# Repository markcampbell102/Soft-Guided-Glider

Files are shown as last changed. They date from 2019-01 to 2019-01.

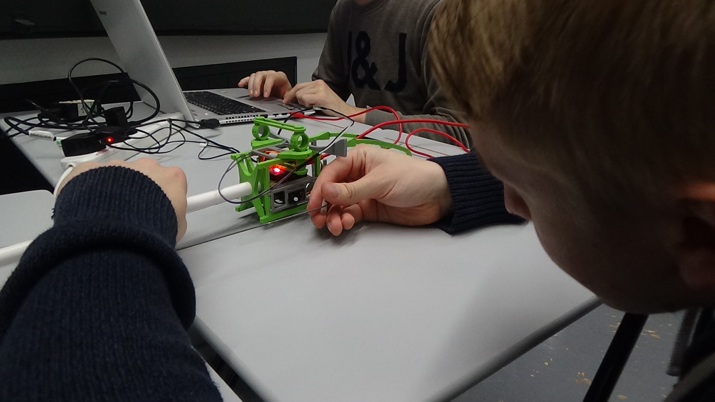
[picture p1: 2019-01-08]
Photos and Videos/Testing/DSC00016.JPG

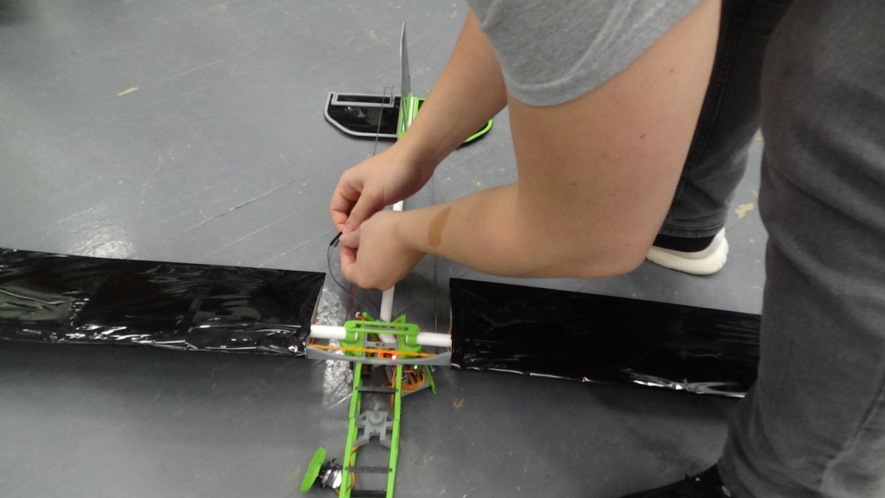
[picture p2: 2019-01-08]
Photos and Videos/Testing/DSC00044.JPG

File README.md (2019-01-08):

# The Soft Guided Glider

During disaster periods there are always areas which are more accessible from the air than from land due to damage to infrastructure after earthquakes or tsunamis. The purpose of this project was to build a low-cost glider that would be able to deliver vital supplies to people in need when they are in these difficult to reach locations. The Glider was designed to be compact, low cost, lightweight and soft. With these attributes it would be able to be thrown from a high altitude and land without damaging its intended cargo, the intended user or itself.

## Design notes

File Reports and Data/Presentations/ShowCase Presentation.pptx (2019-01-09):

## Soft Guided Glider

Andrew Brown, Connor Crabb-Thompson, Jeremy May, Mark Campbell

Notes: Jeremy

## Introduction

- Build a glider that can deliver vital supplies to people in need when they are in hard to reach locations

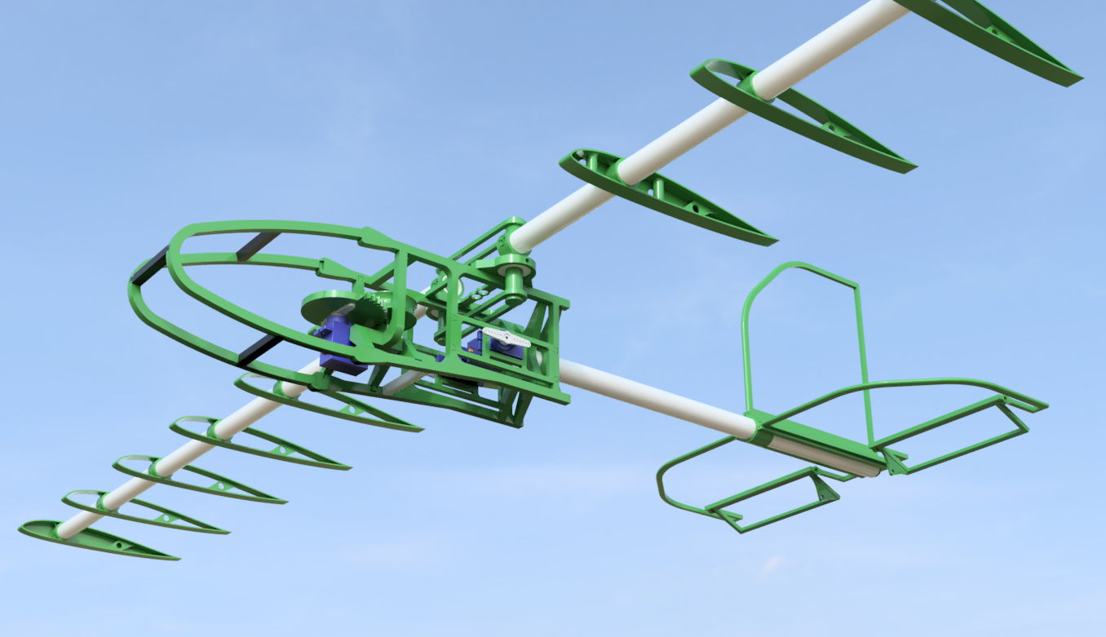
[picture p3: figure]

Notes: Jeremy

## Mechanical Design

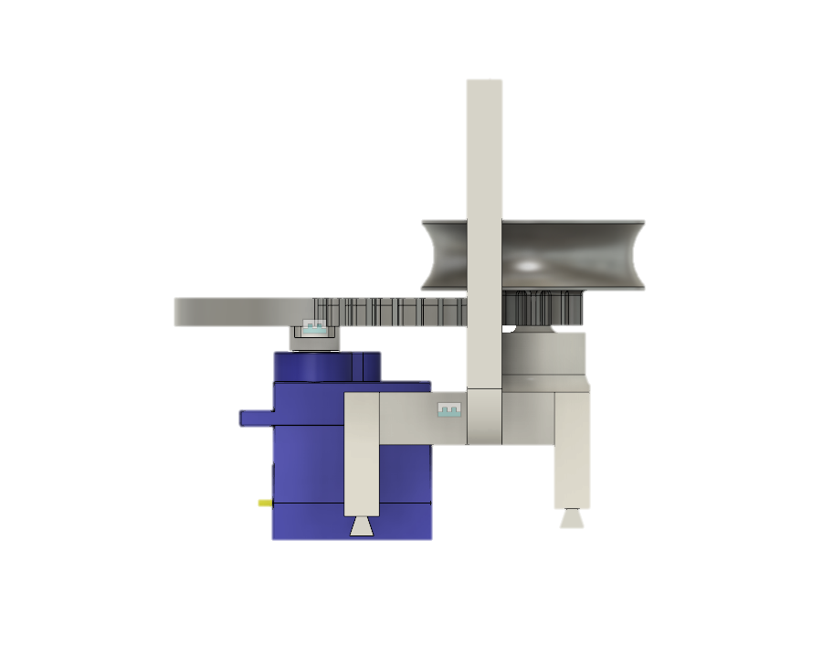
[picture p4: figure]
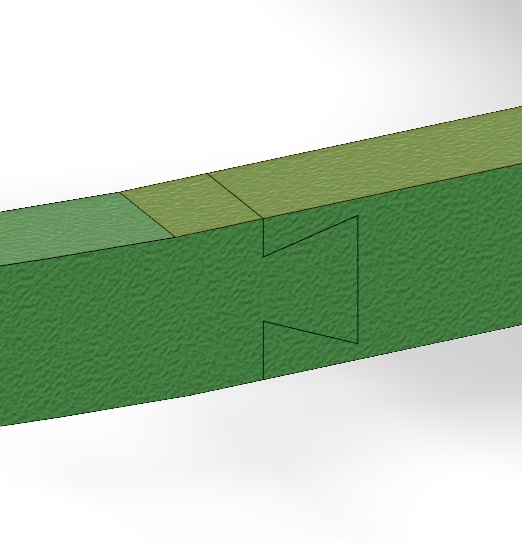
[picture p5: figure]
A picture containing stationary Description generated with very high confidence
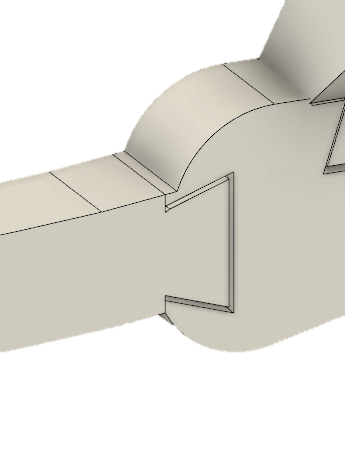
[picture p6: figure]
A picture containing object Description generated with high confidence
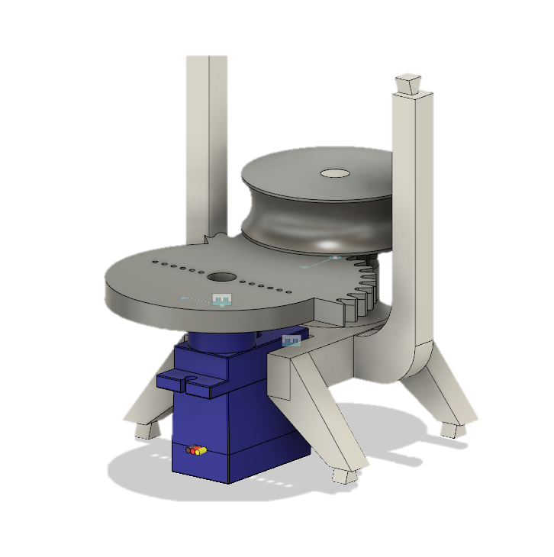
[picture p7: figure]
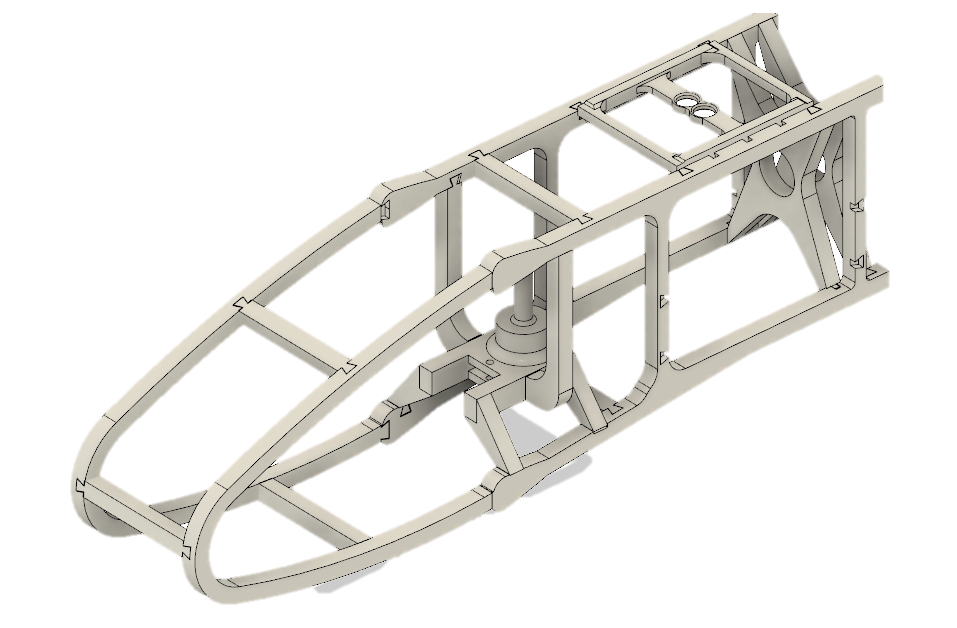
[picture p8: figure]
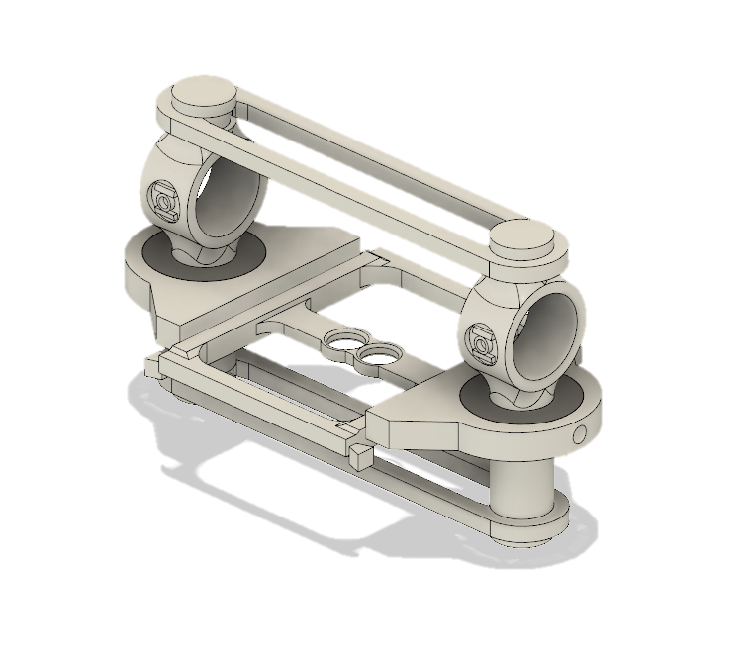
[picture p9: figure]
A picture containing LEGO, toy Description generated with very high confidence

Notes: Andrew

## Integrating Electronics

- Servo Housing has been built into system and connected to elevators
- Circuitry has been miniaturised onto Veroboard

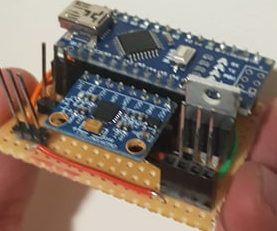
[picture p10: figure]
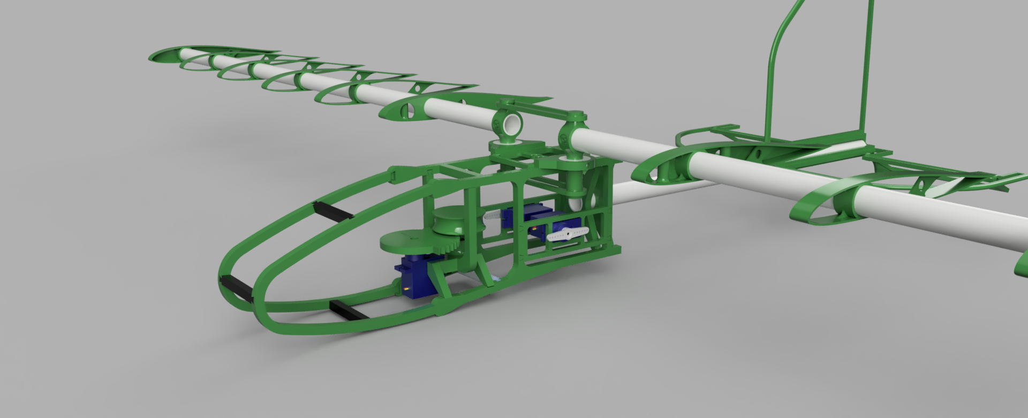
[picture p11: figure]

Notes: Connor

## Testing and Analysis

Analysis:
Finite element analysis

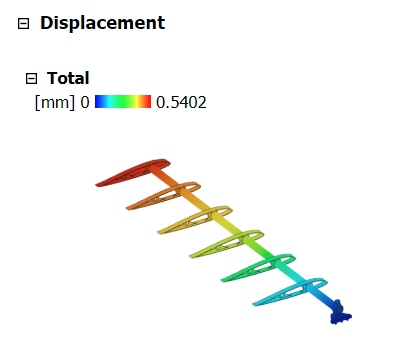
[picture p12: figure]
A close up of a logo Description generated with high confidence
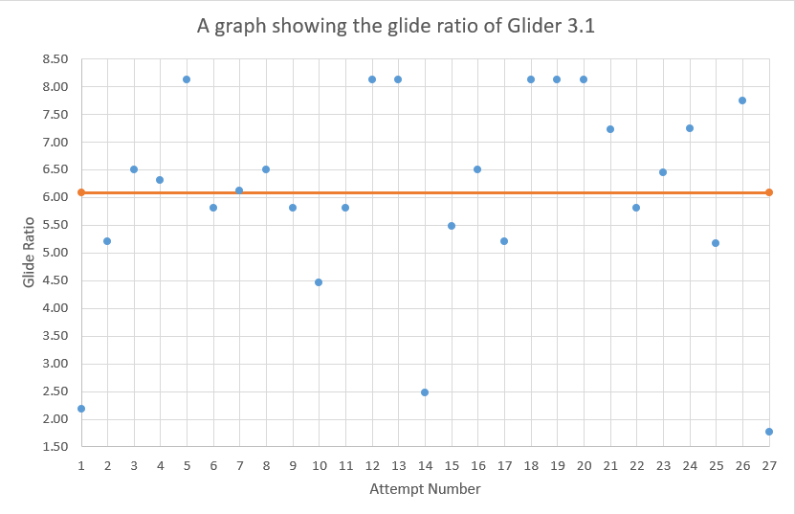
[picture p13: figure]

Testing:
Gliding testing
Compliancy testing
Steering testing

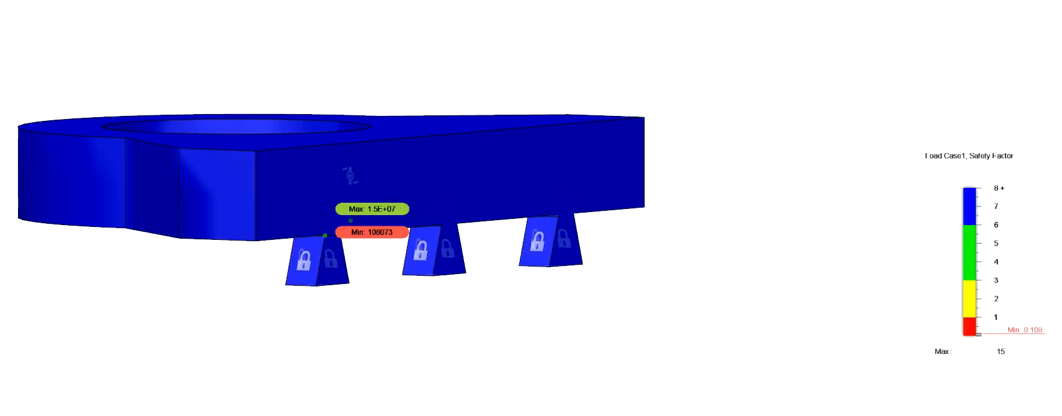
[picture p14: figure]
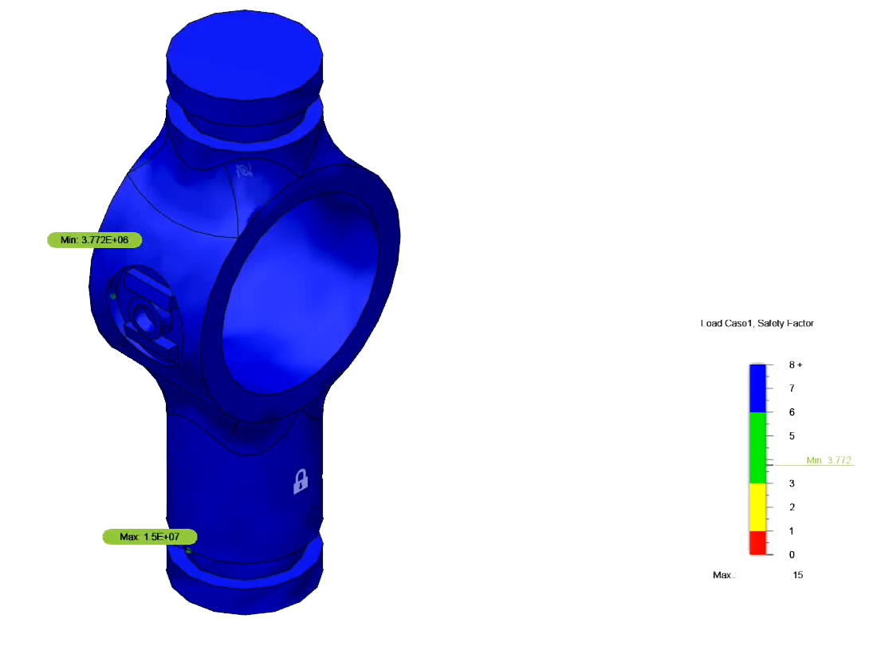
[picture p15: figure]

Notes: Mark

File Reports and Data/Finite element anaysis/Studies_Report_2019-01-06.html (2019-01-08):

Image Width (pixels):

# Wing FEA Report

Analyzed File | wing right v6
Version | Autodesk Fusion 360 (2.0.5119)
Creation Date | 2019-01-06, 12:41:29
Author | Andrew Brown, Mark Campbell

#### Project Properties

Title | Studies
Author | AndrewB

## Simulation Model 1:1

### Study 1 - Static Stress

##### Study Properties

Study Type | Static Stress
Last Modification Date | 2019-01-06, 12:38:17

#### Settings

##### General

Contact Tolerance | 0.1 mm
Remove Rigid Body Modes | No

##### Mesh

Average Element Size (% of model size)
Solids | 10
Scale Mesh Size Per Part | No
Average Element Size (absolute value) | -
Element Order | Parabolic
Create Curved Mesh Elements | Yes
Max. Turn Angle on Curves (Deg.) | 60
Max. Adjacent Mesh Size Ratio | 1.5
Max. Aspect Ratio | 10
Minimum Element Size (% of average size) | 20

##### Adaptive Mesh Refinement

Number of Refinement Steps | 0
Results Convergence Tolerance (%) | 20
Portion of Elements to Refine (%) | 10
Results for Baseline Accuracy | Von Mises Stress

#### Materials

Component | Material | Safety Factor
14mm x 600mm pvc pipe v1:1 | PVC-Piping | Yield Strength
wing 3 airfoil right end v1:1 | ABS Plastic | Yield Strength
wing 3 airfoil v1:1 | ABS Plastic | Yield Strength
wing 3 airfoil v1:2 | ABS Plastic | Yield Strength
wing 3 airfoil v1:3 | ABS Plastic | Yield Strength
wing 3 airfoil v1:4 | ABS Plastic | Yield Strength
wing 3 airfoil RIGHT START v3 v2:1 | ABS Plastic | Yield Strength

##### ABS Plastic

Density | 1.06E-06 kg / mm^3
Young's Modulus | 2240 MPa
Poisson's Ratio | 0.38
Yield Strength | 20 MPa
Ultimate Tensile Strength | 29.6 MPa
Thermal Conductivity | 1.6E-04 W / (mm C)
Thermal Expansion Coefficient | 8.57E-05 / C
Specific Heat | 1500 J / (kg C)

##### PVC-Piping

Density | 1.4E-06 kg / mm^3
Young's Modulus | 3400 MPa
Poisson's Ratio | 0.4
Yield Strength | 46.53 MPa
Ultimate Tensile Strength | 52.36 MPa
Thermal Conductivity | 0.001 W / (mm C)
Thermal Expansion Coefficient | 5E-07 / C
Specific Heat | 100 J / (kg C)

#### Contacts

##### Bonded

Name

[S] Bonded1 [14mm x 600mm pvc pipe v1:1||wing 3 airfoil right end v1:1]

[S] Bonded2 [14mm x 600mm pvc pipe v1:1||wing 3 airfoil RIGHT START v3 v2:1]

[S] Bonded3 [14mm x 600mm pvc pipe v1:1||wing 3 airfoil v1:4]

[S] Bonded4 [14mm x 600mm pvc pipe v1:1||wing 3 airfoil v1:3]

[S] Bonded5 [14mm x 600mm pvc pipe v1:1||wing 3 airfoil v1:2]

[S] Bonded6 [14mm x 600mm pvc pipe v1:1||wing 3 airfoil v1:1]

#### Mesh

Type | Nodes | Elements
Solids | 42074 | 19665

#### Load Case1

#### Constraints

##### Fixed1

Type | Fixed
Ux | Yes
Uy | Yes
Uz | Yes

###### Selected Entities

For correct interpretation of this image use e.g. IE9, Chrome, Safari, Firefox

#### Loads

##### Gravity

Type | Gravity
Magnitude | 9.807 m / s^2
X Value | 0 m / s^2
Y Value | -9.807 m / s^2
Z Value | 0 m / s^2

###### Selected Entities

For correct interpretation of this image use e.g. IE9, Chrome, Safari, Firefox

#### Results

##### Result Summary

Name | Minimum | Maximum
Safety Factor
Safety Factor (Per Body) | 15 | 15
Stress
Von Mises | 1.04E-06 MPa | 1.233 MPa
1st Principal | -0.4449 MPa | 1.876 MPa
3rd Principal | -1.423 MPa | 0.5272 MPa
Normal XX | -0.6099 MPa | 0.8494 MPa
Normal YY | -0.539 MPa | 0.6461 MPa
Normal ZZ | -1.383 MPa | 1.845 MPa
Shear XY | -0.1186 MPa | 0.09273 MPa
Shear YZ | -0.3367 MPa | 0.4469 MPa
Shear ZX | -0.3456 MPa | 0.3116 MPa
Displacement
Total | 0 mm | 1.149 mm
X | -2.596E-04 mm | 0.2115 mm
Y | -1.128 mm | 2.035E-05 mm
Z | -0.02293 mm | 0.06109 mm
Reaction Force
Total | 0 N | 1.872 N
X | -0.5288 N | 0.5612 N
Y | -0.9159 N | 1.152 N
Z | -1.37 N | 1.411 N
Strain
Equivalent | 7.027E-10 | 7.318E-04
1st Principal | 5.879E-10 | 8.061E-04
3rd Principal | -5.086E-04 | 4.124E-09
Normal XX | -8.495E-05 | 9.184E-05
Normal YY | -1.987E-04 | 1.058E-04
Normal ZZ | -4.224E-04 | 5.918E-04
Shear XY | -1.461E-04 | 1.143E-04
Shear YZ | -4.148E-04 | 4.401E-04
Shear ZX | -4.259E-04 | 3.839E-04
Contact Pressure
Total | 0 MPa | 0.5963 MPa
X | -0.07875 MPa | 0.08341 MPa
Y | -0.1702 MPa | 0.5621 MPa
Z | -0.1929 MPa | 0.1869 MPa

##### Safety Factor

###### Safety Factor (Per Body)

0 8

For correct interpretation of this image use e.g. IE9, Chrome, Safari, Firefox

##### Stress

###### Von Mises

[MPa] 0 1.233

For correct interpretation of this image use e.g. IE9, Chrome, Safari, Firefox

###### 1st Principal

[MPa] -0.445 1.876

For correct interpretation of this image use e.g. IE9, Chrome, Safari, Firefox

###### 3rd Principal

[MPa] -1.423 0.527

For correct interpretation of this image use e.g. IE9, Chrome, Safari, Firefox

##### Displacement

###### Total

[mm] 0 1.149

For correct interpretation of this image use e.g. IE9, Chrome, Safari, Firefox

Image Width (pixels):

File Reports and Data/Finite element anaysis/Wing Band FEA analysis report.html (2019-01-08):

Image Width (pixels):

# Wing Band FEA analysis report

Analyzed File | wing band v7
Version | Autodesk Fusion 360 (2.0.5119)
Creation Date | 2019-01-06, 11:46:38
Author | Andrew Brown, Mark Campbell

#### Project Properties

Title | Studies
Author | AndrewB

## Simulation Model 1:1

### Study 1 - Static Stress

##### Study Properties

Study Type | Static Stress
Last Modification Date | 2019-01-05, 18:14:45

#### Settings

##### General

Contact Tolerance | 0.1 mm
Remove Rigid Body Modes | No

##### Mesh

Average Element Size (% of model size)
Solids | 10
Scale Mesh Size Per Part | No
Average Element Size (absolute value) | -
Element Order | Parabolic
Create Curved Mesh Elements | Yes
Max. Turn Angle on Curves (Deg.) | 60
Max. Adjacent Mesh Size Ratio | 1.5
Max. Aspect Ratio | 10
Minimum Element Size (% of average size) | 20

##### Adaptive Mesh Refinement

Number of Refinement Steps | 0
Results Convergence Tolerance (%) | 20
Portion of Elements to Refine (%) | 10
Results for Baseline Accuracy | Von Mises Stress

#### Materials

Component | Material | Safety Factor
Body1 | ABS Plastic | Yield Strength

##### ABS Plastic

Density | 1.06E-06 kg / mm^3
Young's Modulus | 2240 MPa
Poisson's Ratio | 0.38
Yield Strength | 20 MPa
Ultimate Tensile Strength | 29.6 MPa
Thermal Conductivity | 1.6E-04 W / (mm C)
Thermal Expansion Coefficient | 8.57E-05 / C
Specific Heat | 1500 J / (kg C)

#### Contacts

#### Mesh

Type | Nodes | Elements
Solids | 2045 | 1021

#### Load Case1

#### Constraints

##### Fixed1

Type | Fixed
Ux | Yes
Uy | Yes
Uz | Yes

###### Selected Entities

For correct interpretation of this image use e.g. IE9, Chrome, Safari, Firefox

#### Loads

##### Force1

Type | Force
Magnitude | 12 N
X Value | -12 N
Y Value | 0 N
Z Value | 0 N
X Angle | 0 deg
Y Angle | 0 deg
Z Angle | 0 deg
Force Per Entity | No

###### Selected Entities

For correct interpretation of this image use e.g. IE9, Chrome, Safari, Firefox

##### Force2

Type | Force
Magnitude | 12 N
X Value | 12 N
Y Value | 0 N
Z Value | 0 N
X Angle | 0 deg
Y Angle | 0 deg
Z Angle | 0 deg
Force Per Entity | No

###### Selected Entities

For correct interpretation of this image use e.g. IE9, Chrome, Safari, Firefox

#### Results

##### Result Summary

Name | Minimum | Maximum
Safety Factor
Safety Factor (Per Body) | 15 | 15
Stress
Von Mises | 2.283E-06 MPa | 0.6002 MPa
1st Principal | -0.1353 MPa | 0.6666 MPa
3rd Principal | -0.5343 MPa | 0.1268 MPa
Normal XX | -0.3974 MPa | 0.6541 MPa
Normal YY | -0.4178 MPa | 0.4562 MPa
Normal ZZ | -0.2417 MPa | 0.2879 MPa
Shear XY | -0.3285 MPa | 0.3107 MPa
Shear YZ | -0.05948 MPa | 0.06786 MPa
Shear ZX | -0.2087 MPa | 0.2208 MPa
Displacement
Total | 0 mm | 9.274E-04 mm
X | -8.42E-04 mm | 8.679E-04 mm
Y | -2.073E-04 mm | 3.267E-04 mm
Z | -2.113E-04 mm | 1.965E-04 mm
Reaction Force
Total | 0 N | 1.06 N
X | -0.9213 N | 0.8655 N
Y | -0.6553 N | 0.6005 N
Z | -0.1777 N | 0.1644 N
Strain
Equivalent | 1.816E-09 | 4.677E-04
1st Principal | 1.214E-09 | 4.145E-04
3rd Principal | -3.953E-04 | -1.838E-09
Normal XX | -1.701E-04 | 2.668E-04
Normal YY | -1.081E-04 | 1.167E-04
Normal ZZ | -1.094E-04 | 6.626E-05
Shear XY | -4.048E-04 | 3.828E-04
Shear YZ | -7.329E-05 | 8.361E-05
Shear ZX | -2.572E-04 | 2.72E-04

##### Safety Factor

###### Safety Factor (Per Body)

0 8

For correct interpretation of this image use e.g. IE9, Chrome, Safari, Firefox

##### Stress

###### Von Mises

[MPa] 0 0.6002

For correct interpretation of this image use e.g. IE9, Chrome, Safari, Firefox

###### 1st Principal

[MPa] -0.1353 0.6666

For correct interpretation of this image use e.g. IE9, Chrome, Safari, Firefox

###### 3rd Principal

[MPa] -0.5343 0.1268

For correct interpretation of this image use e.g. IE9, Chrome, Safari, Firefox

##### Displacement

###### Total

[mm] 0 9.274E-04

For correct interpretation of this image use e.g. IE9, Chrome, Safari, Firefox

Image Width (pixels):

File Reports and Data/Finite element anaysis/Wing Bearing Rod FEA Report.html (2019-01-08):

Image Width (pixels):

# Wing Bearing Rod FEA Report

Analyzed File | green lantern v11
Version | Autodesk Fusion 360 (2.0.5119)
Creation Date | 2019-01-06, 11:47:30
Author | Andrew Brown, Mark Campbell

#### Project Properties

Title | Studies
Author | mqcampbell

## Simulation Model 1:1

### Study 2 - Static Stress

##### Study Properties

Study Type | Static Stress
Last Modification Date | 2019-01-05, 18:17:33

#### Settings

##### General

Contact Tolerance | 0.1 mm
Remove Rigid Body Modes | No

##### Mesh

Average Element Size (% of model size)
Solids | 10
Scale Mesh Size Per Part | No
Average Element Size (absolute value) | -
Element Order | Parabolic
Create Curved Mesh Elements | Yes
Max. Turn Angle on Curves (Deg.) | 60
Max. Adjacent Mesh Size Ratio | 1.5
Max. Aspect Ratio | 10
Minimum Element Size (% of average size) | 20

##### Adaptive Mesh Refinement

Number of Refinement Steps | 0
Results Convergence Tolerance (%) | 20
Portion of Elements to Refine (%) | 10
Results for Baseline Accuracy | Von Mises Stress

#### Materials

Component | Material | Safety Factor
Body1 | ABS Plastic | Yield Strength

##### ABS Plastic

Density | 1.06E-06 kg / mm^3
Young's Modulus | 2240 MPa
Poisson's Ratio | 0.38
Yield Strength | 20 MPa
Ultimate Tensile Strength | 29.6 MPa
Thermal Conductivity | 1.6E-04 W / (mm C)
Thermal Expansion Coefficient | 8.57E-05 / C
Specific Heat | 1500 J / (kg C)

#### Contacts

#### Mesh

Type | Nodes | Elements
Solids | 2573 | 1341

#### Load Case1

#### Constraints

##### Fixed1

Type | Fixed
Ux | Yes
Uy | Yes
Uz | Yes

###### Selected Entities

For correct interpretation of this image use e.g. IE9, Chrome, Safari, Firefox

#### Loads

##### Moment1

Type | Moment
Magnitude | 192 N mm
X Value | -192 N mm
Y Value | 0 N mm
Z Value | 4.263E-14 N mm
X Angle | 0 deg
Y Angle | 0 deg
Z Angle | 0 deg

###### Selected Entities

For correct interpretation of this image use e.g. IE9, Chrome, Safari, Firefox

#### Results

##### Result Summary

Name | Minimum | Maximum
Safety Factor
Safety Factor (Per Body) | 4.491 | 15
Stress
Von Mises | 3.796E-08 MPa | 4.453 MPa
1st Principal | -0.7836 MPa | 4.472 MPa
3rd Principal | -4.612 MPa | 0.7673 MPa
Normal XX | -1.626 MPa | 1.665 MPa
Normal YY | -4.027 MPa | 4.138 MPa
Normal ZZ | -2.213 MPa | 2.249 MPa
Shear XY | -1.634 MPa | 1.558 MPa
Shear YZ | -1.694 MPa | 1.106 MPa
Shear ZX | -1.276 MPa | 1.217 MPa
Displacement
Total | 0 mm | 0.1566 mm
X | -0.01783 mm | 0.01843 mm
Y | -0.0398 mm | 0.03999 mm
Z | -0.1523 mm | 3.496E-04 mm
Reaction Force
Total | 0 N | 4.381 N
X | -2.166 N | 2.091 N
Y | -3.311 N | 3.846 N
Z | -1.247 N | 1.963 N
Strain
Equivalent | 2.663E-11 | 0.003043
1st Principal | 2.219E-11 | 0.002726
3rd Principal | -0.003147 | -2.207E-11
Normal XX | -7.456E-04 | 7.316E-04
Normal YY | -0.001668 | 0.00174
Normal ZZ | -6.567E-04 | 7.107E-04
Shear XY | -0.002013 | 0.00192
Shear YZ | -0.002088 | 0.001363
Shear ZX | -0.001572 | 0.001499

##### Safety Factor

###### Safety Factor (Per Body)

0 8

For correct interpretation of this image use e.g. IE9, Chrome, Safari, Firefox

##### Stress

###### Von Mises

[MPa] 0 4.453

For correct interpretation of this image use e.g. IE9, Chrome, Safari, Firefox

###### 1st Principal

[MPa] -0.784 4.472

For correct interpretation of this image use e.g. IE9, Chrome, Safari, Firefox

###### 3rd Principal

[MPa] -4.612 0.767

For correct interpretation of this image use e.g. IE9, Chrome, Safari, Firefox

##### Displacement

###### Total

[mm] 0 0.1566

For correct interpretation of this image use e.g. IE9, Chrome, Safari, Firefox

Image Width (pixels):

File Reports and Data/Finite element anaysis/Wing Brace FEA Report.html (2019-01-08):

Image Width (pixels):

# wing brace FEA report

Analyzed File | wing brace v10
Version | Autodesk Fusion 360 (2.0.5119)
Creation Date | 2019-01-06, 13:33:17
Author | Andrew Brown, Mark Campbell

#### Project Properties

Title | Studies
Author | AndrewB

## Simulation Model 1:1

### Study 2 - Static Stress

##### Study Properties

Study Type | Static Stress
Last Modification Date | 2019-01-06, 13:30:13

#### Settings

##### General

Contact Tolerance | 0.1 mm
Remove Rigid Body Modes | No

##### Mesh

Average Element Size (% of model size)
Solids | 10
Scale Mesh Size Per Part | No
Average Element Size (absolute value) | -
Element Order | Parabolic
Create Curved Mesh Elements | Yes
Max. Turn Angle on Curves (Deg.) | 60
Max. Adjacent Mesh Size Ratio | 1.5
Max. Aspect Ratio | 10
Minimum Element Size (% of average size) | 20

##### Adaptive Mesh Refinement

Number of Refinement Steps | 0
Results Convergence Tolerance (%) | 20
Portion of Elements to Refine (%) | 10
Results for Baseline Accuracy | Von Mises Stress

#### Materials

Component | Material | Safety Factor
Body5 | ABS Plastic | Yield Strength

##### ABS Plastic

Density | 1.06E-06 kg / mm^3
Young's Modulus | 2240 MPa
Poisson's Ratio | 0.38
Yield Strength | 20 MPa
Ultimate Tensile Strength | 29.6 MPa
Thermal Conductivity | 1.6E-04 W / (mm C)
Thermal Expansion Coefficient | 8.57E-05 / C
Specific Heat | 1500 J / (kg C)

#### Contacts

#### Mesh

Type | Nodes | Elements
Solids | 12501 | 7020

#### Load Case1

#### Constraints

##### Fixed2

Type | Fixed
Ux | Yes
Uy | Yes
Uz | Yes

###### Selected Entities

For correct interpretation of this image use e.g. IE9, Chrome, Safari, Firefox

#### Loads

##### Gravity

Type | Gravity
Magnitude | 9.807 m / s^2
X Value | 0 m / s^2
Y Value | -9.807 m / s^2
Z Value | 0 m / s^2

###### Selected Entities

For correct interpretation of this image use e.g. IE9, Chrome, Safari, Firefox

##### Force1

Type | Force
Magnitude | 1 N
X Value | 0 N
Y Value | 0 N
Z Value | 1 N
Force Per Entity | No

###### Selected Entities

For correct interpretation of this image use e.g. IE9, Chrome, Safari, Firefox

#### Results

##### Result Summary

Name | Minimum | Maximum
Safety Factor
Safety Factor (Per Body) | 15 | 15
Stress
Von Mises | 1.461E-18 MPa | 0.7413 MPa
1st Principal | -0.0411 MPa | 0.9361 MPa
3rd Principal | -0.4175 MPa | 0.3906 MPa
Normal XX | -0.2087 MPa | 0.5432 MPa
Normal YY | -0.2808 MPa | 0.5742 MPa
Normal ZZ | -0.4055 MPa | 0.6938 MPa
Shear XY | -0.1047 MPa | 0.07226 MPa
Shear YZ | -0.2261 MPa | 0.1931 MPa
Shear ZX | -0.1428 MPa | 0.1479 MPa
Displacement
Total | 0 mm | 0.06755 mm
X | -0.001484 mm | 1.382E-04 mm
Y | -3.579E-04 mm | 0.06277 mm
Z | -0.0246 mm | 0.02499 mm
Reaction Force
Total | 0 N | 0.2882 N
X | -0.03586 N | 0.04169 N
Y | -0.04169 N | 0.08177 N
Z | -0.2768 N | 0.282 N
Strain
Equivalent | 0 | 4.135E-04
1st Principal | 0 | 4.571E-04
3rd Principal | -2.445E-04 | 0
Normal XX | -9.423E-05 | 6.521E-05
Normal YY | -1.871E-04 | 6.47E-05
Normal ZZ | -1.702E-04 | 2.8E-04
Shear XY | -1.29E-04 | 8.904E-05
Shear YZ | -2.786E-04 | 2.38E-04
Shear ZX | -1.76E-04 | 1.823E-04

##### Safety Factor

###### Safety Factor (Per Body)

0 8

For correct interpretation of this image use e.g. IE9, Chrome, Safari, Firefox

##### Stress

###### Von Mises

[MPa] 0 0.7413

For correct interpretation of this image use e.g. IE9, Chrome, Safari, Firefox

###### 1st Principal

[MPa] -0.0411 0.9361

For correct interpretation of this image use e.g. IE9, Chrome, Safari, Firefox

###### 3rd Principal

[MPa] -0.4175 0.3906

For correct interpretation of this image use e.g. IE9, Chrome, Safari, Firefox

##### Displacement

###### Total

[mm] 0 0.06755

For correct interpretation of this image use e.g. IE9, Chrome, Safari, Firefox

Image Width (pixels):

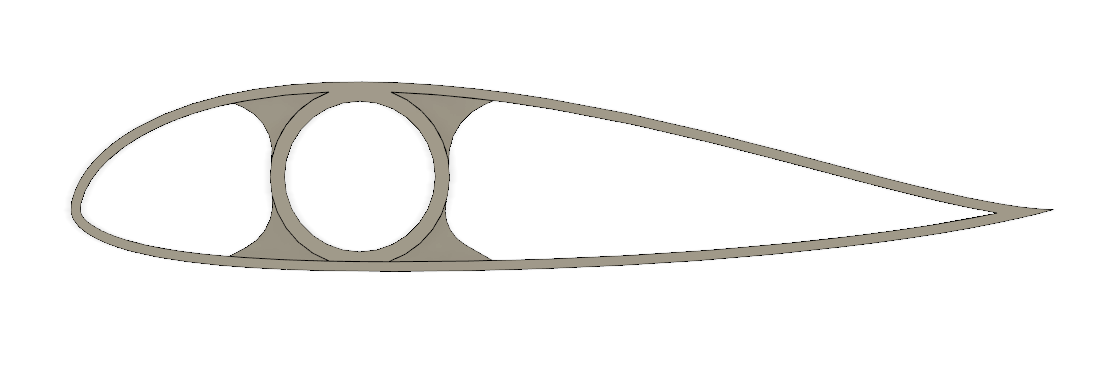
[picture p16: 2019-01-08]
Photos and Videos/Mechanical Models/Aerofoil/prototype/Aerofoil 1 side.PNG

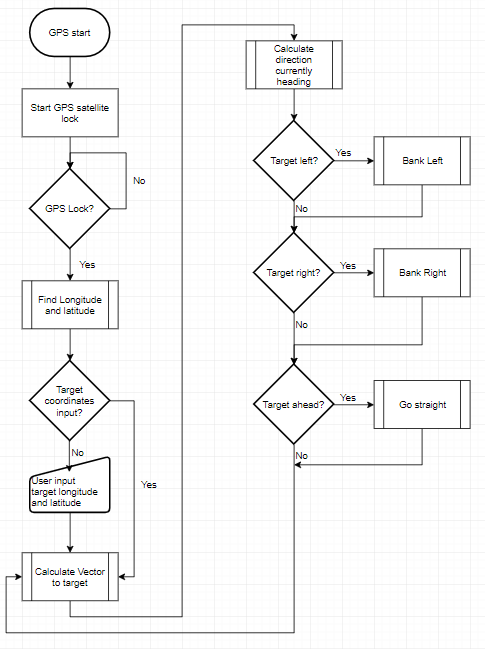
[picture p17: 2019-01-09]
Electronics/Localisation/GPS Flowchart.PNG

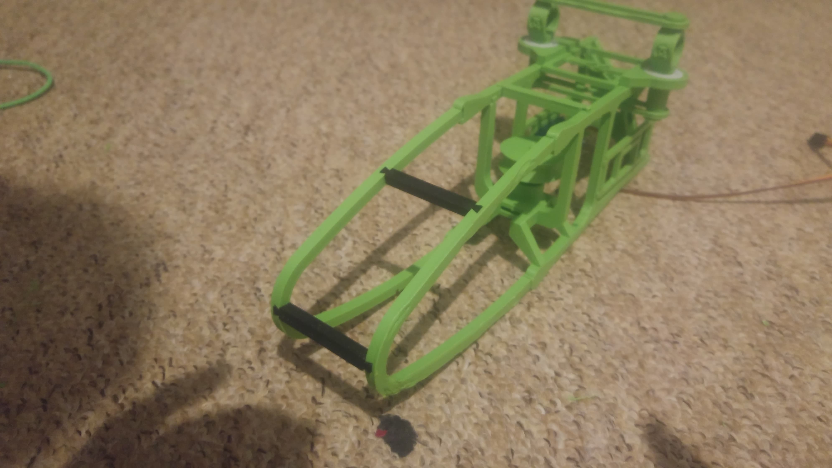
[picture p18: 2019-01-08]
Photos and Videos/Mechanical Models/Body/body v3/49678581_937155589824171_4841866462714920960_n.jpg

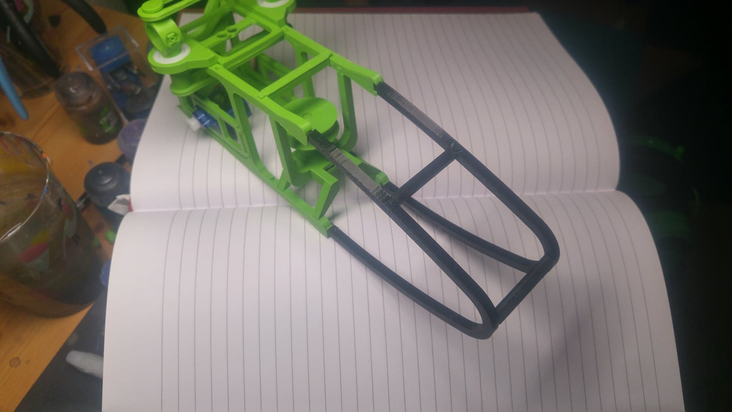
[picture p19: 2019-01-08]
Photos and Videos/Mechanical Models/Body/body v3/49845082_1233951370087210_7048269515758501888_n.jpg

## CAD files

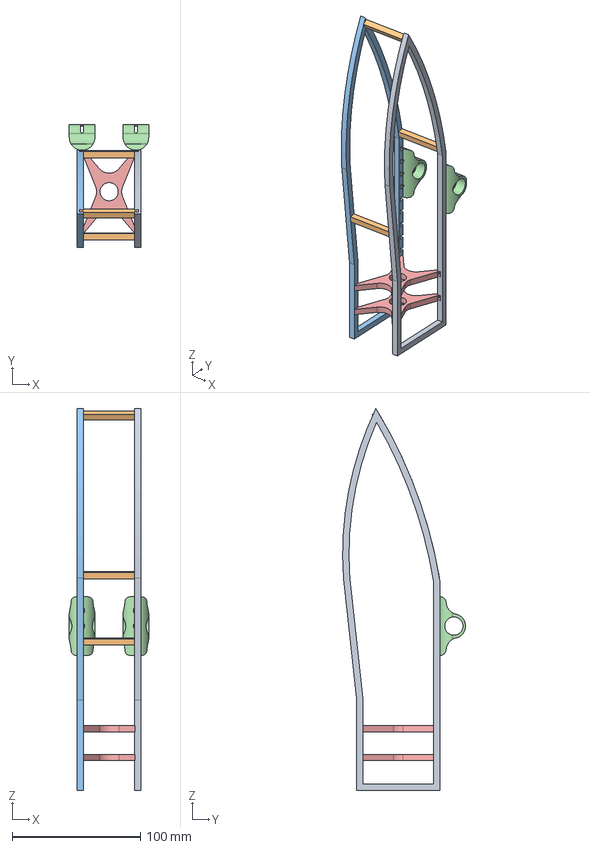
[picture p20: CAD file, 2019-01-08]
Mechanicals/assembalies/body 2/body assembly 2.stp
62.0 x 95.8 x 297.9 mm
body side mirrored v3 x 2
standard strut x 3
body side
wing attachment x 2
x beam x 2

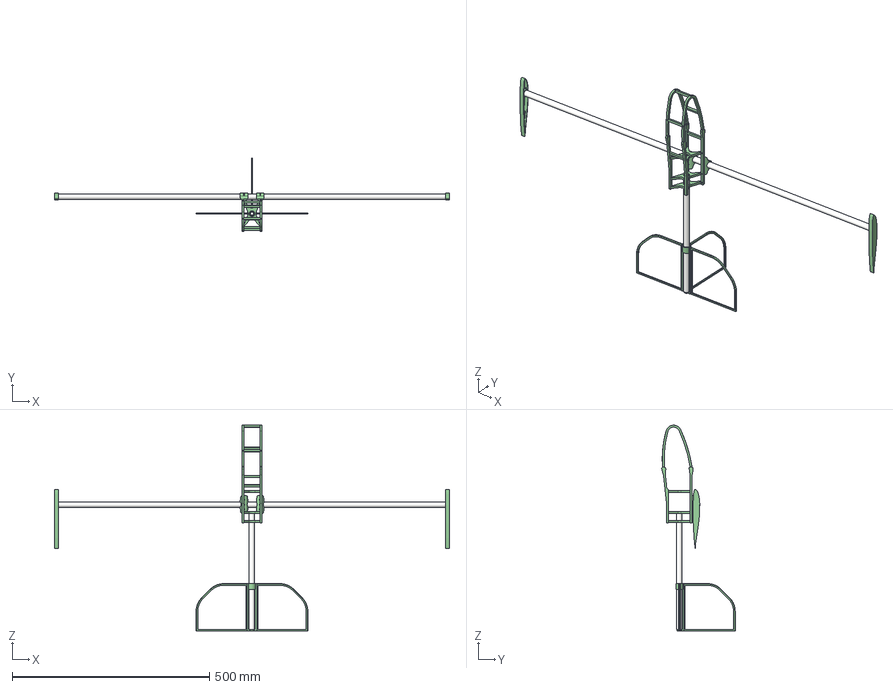
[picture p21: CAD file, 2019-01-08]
Mechanicals/assembalies/body 3.1/Test assembly.stp
1002.0 x 186.6 x 522.0 mm
body right side back
body side right front
x beam x 3
body left side back
body side left front
standard strut x 5
wing attachment x 2
14mm x 1000mm rod
wing 3 airfoil left end
wing 3 airfoil right end
14mmx 300mm
rod attachment 2
horzontal fin x 3

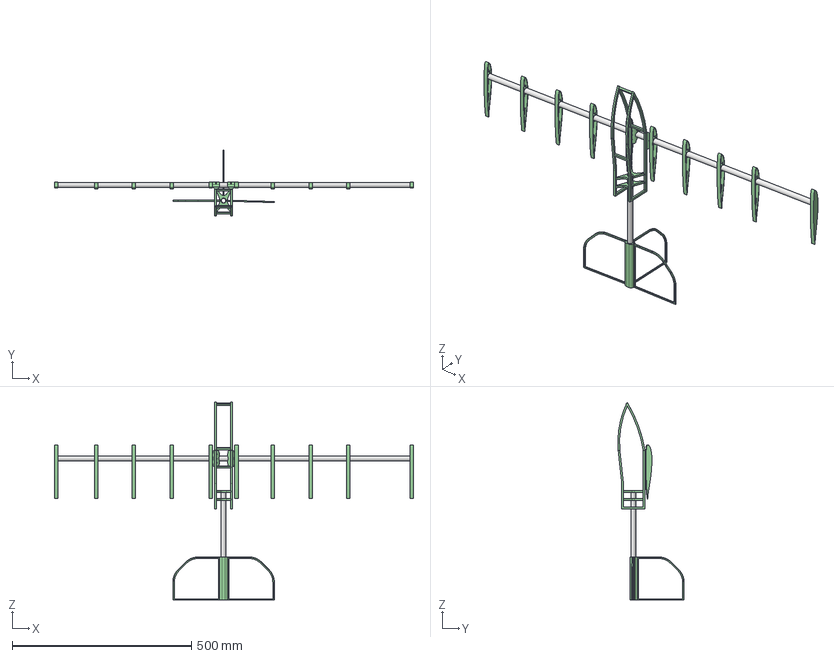
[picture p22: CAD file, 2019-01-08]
Mechanicals/assembalies/body 3/assembly 3.stp
1002.0 x 185.1 x 552.1 mm
body left side back
body side left front
standard strut x 3
x beam x 2
body right side back
body side right front
wing attachment x 2
14mm x 1000mm rod
wing 3 airfoil x 8
wing 3 airfoil right end
wing 3 airfoil left end
14mmx 300mm
rod attachment
horzontal fin x 3

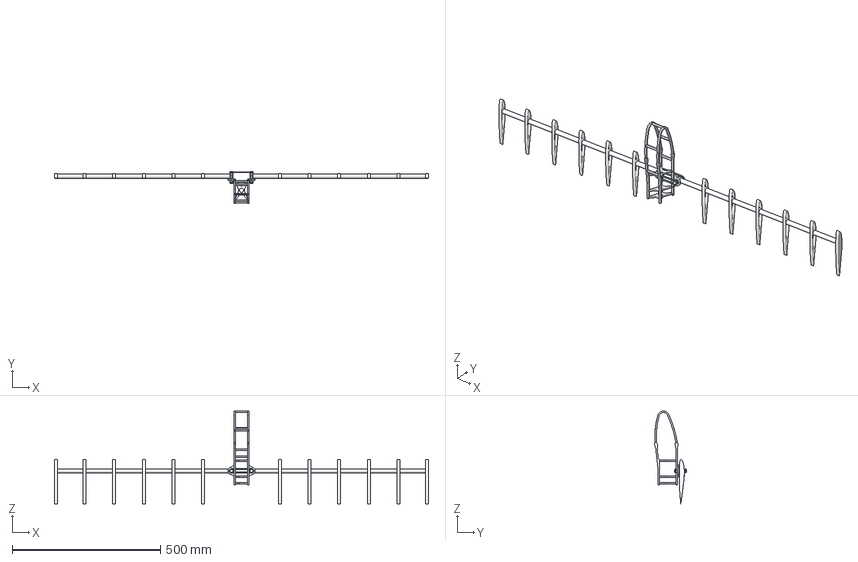
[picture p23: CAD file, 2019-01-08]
Mechanicals/assembalies/body 4/Assembly 5.stp
1259.9 x 108.2 x 313.0 mm
body left side back v2
body side left front v2
standard strut v2 x 5
x beam v3 x 3
body side right front v2
body right side back v2
wing bearing mount right v7 x 2
10mm x 15mm x 4mm bearing v1 x 2
green lantern v4 x 2
wing band v2 x 2
14mm x 600mm pvc pipe v1 x 2
wing 3 airfoil right end v1
wing 3 airfoil v1 x 10
wing 3 airfoil left end v3

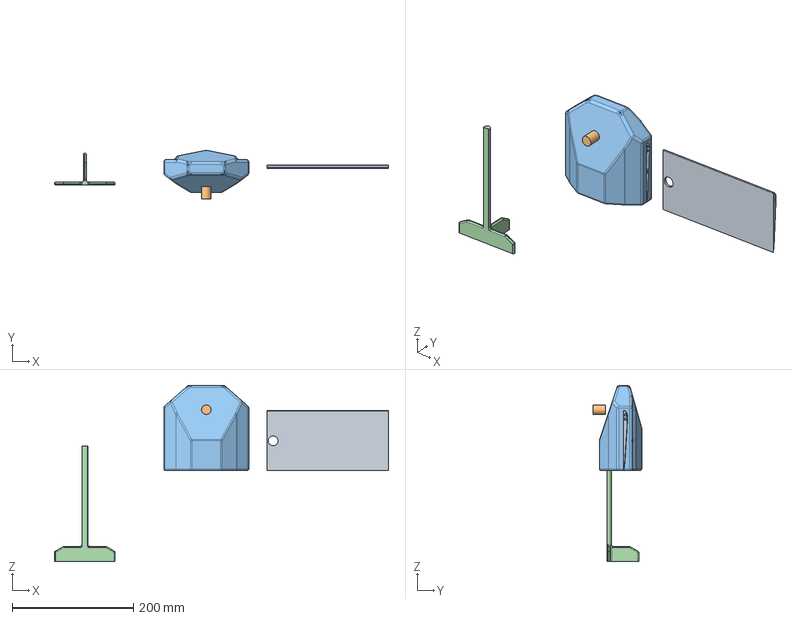
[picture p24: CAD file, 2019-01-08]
Mechanicals/Body/body 1/Body Main.stp
550.0 x 79.9 x 290.0 mm
wing mount point mirror
Pin

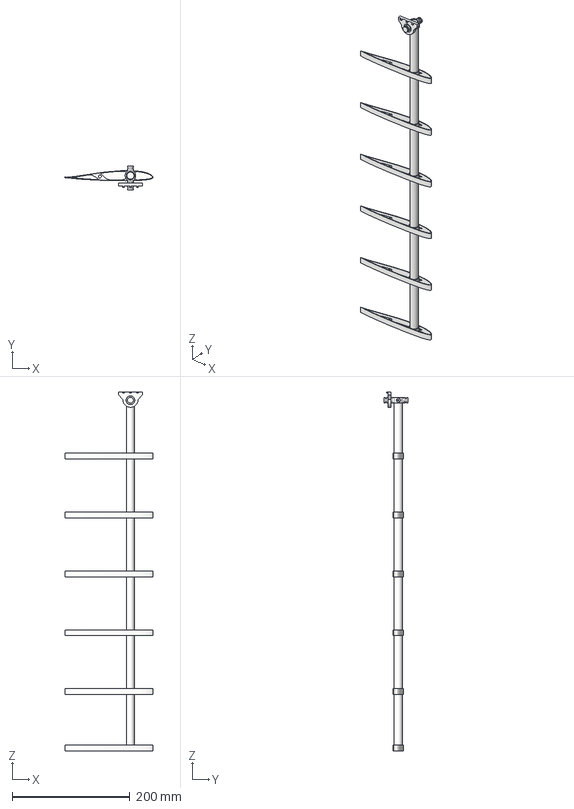
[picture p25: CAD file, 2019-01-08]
Mechanicals/Simulation/Wing Hing assembly.stp
150.0 x 40.0 x 610.0 mm
green lantern v7
14mm x 600mm pvc pipe v1
wing 3 airfoil left end v3
wing 3 airfoil v1 x 5
wing bearing mount right v11
10mm x 15mm x 4mm bearing v1

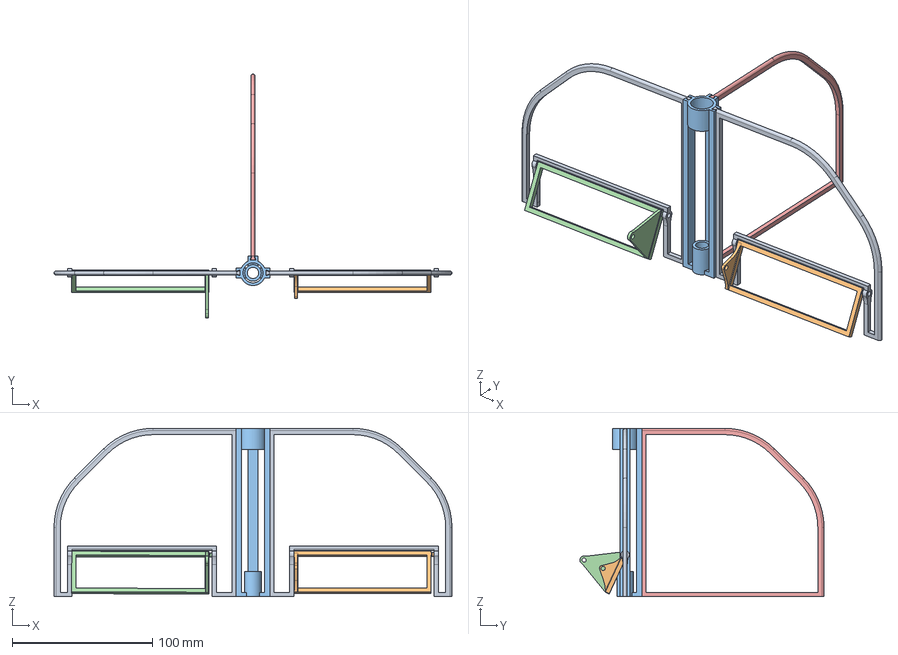
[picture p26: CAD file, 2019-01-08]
Mechanicals/Tails/tail 2/assembly.stp
283.8 x 174.1 x 120.0 mm
vertical fin x 2
horizontal move fin right
rod attachment 2
horizontal move fin left
horzontal fin

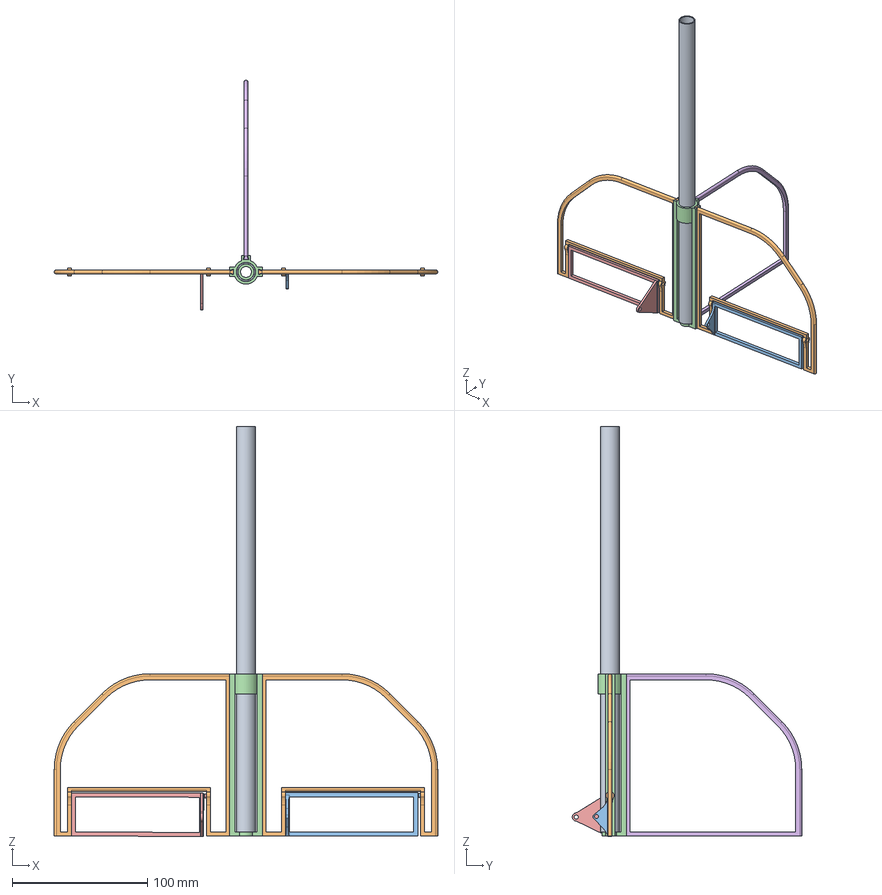
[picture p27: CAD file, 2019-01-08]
Mechanicals/Tails/tail 2/tail assembly full.stp
283.8 x 169.9 x 303.4 mm
14mmx 300mm
vertical fin x 2
horizontal move fin right
rod attachment 2
horizontal move fin left
horzontal fin

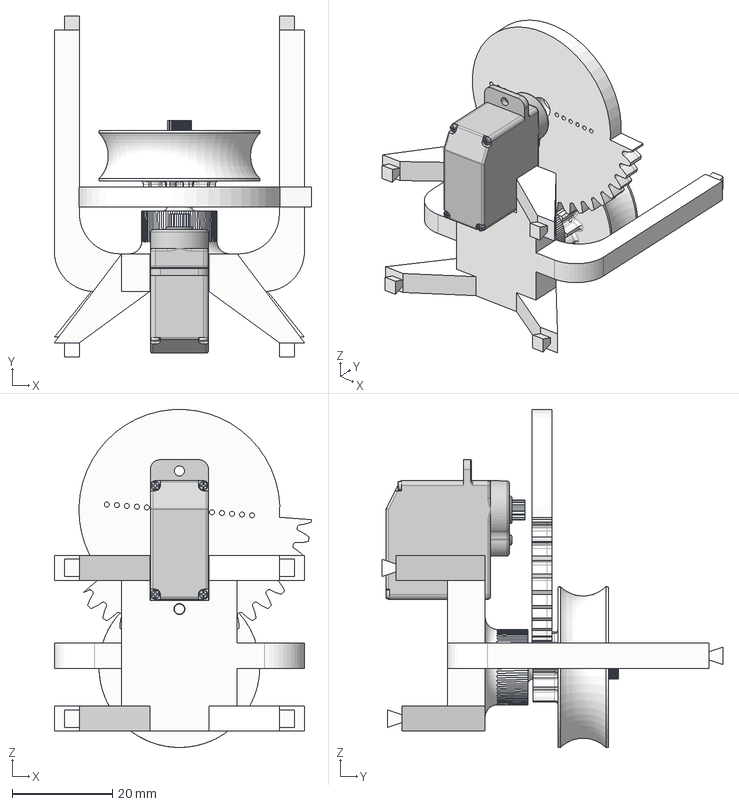
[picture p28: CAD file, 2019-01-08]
Mechanicals/assembalies/folder servo mount.stp
51.2 x 67.8 x 67.3 mm
folding gear mount
Spur Gear (42 teeth)
Emax ES08A

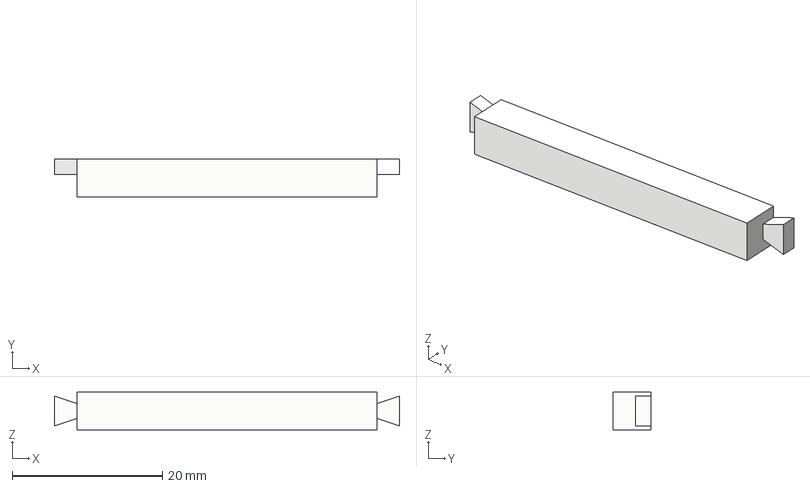
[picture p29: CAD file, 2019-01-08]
Mechanicals/Body/Body 2/standard strut.stp
46.0 x 5.00 x 5.00 mm

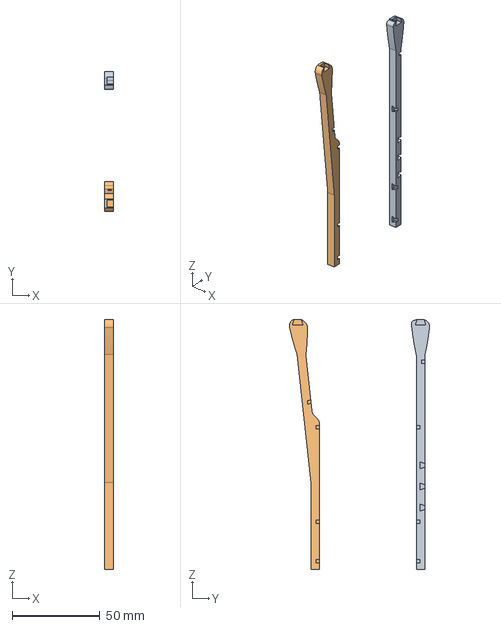
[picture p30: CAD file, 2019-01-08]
Mechanicals/Body/Body 3.1/body right side back.stp
5.00 x 79.8 x 142.2 mm

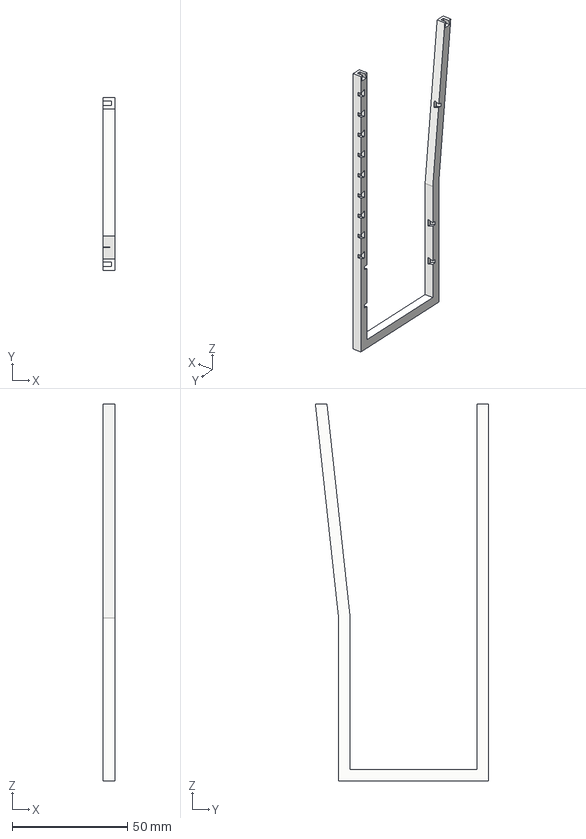
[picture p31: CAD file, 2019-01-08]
Mechanicals/Body/Body 3/body left side back.stp
5.00 x 75.0 x 163.2 mm

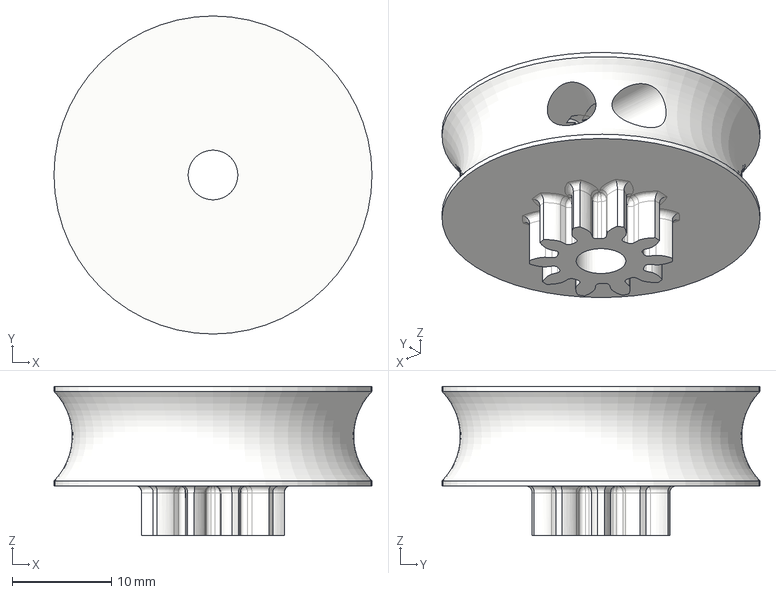
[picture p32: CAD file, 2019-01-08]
Mechanicals/Body/body 4/driven gear.stp
32.0 x 32.0 x 15.0 mm

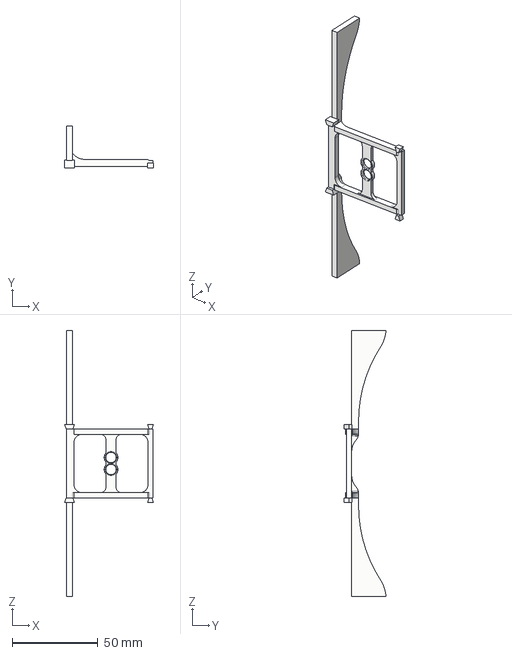
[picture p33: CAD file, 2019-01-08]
Mechanicals/Body/body 5/wing brace.stp
51.8 x 24.5 x 154.9 mm

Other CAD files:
Mechanicals/downloads/9g servo.stp
Mechanicals/Final 3D Model/Parts/servos/9g servo.stp
Mechanicals/Final 3D Model/Parts/wings/wing 3 airfoil RIGHT START v3.stp
Mechanicals/Body/Body 2/body right side front.obj
Mechanicals/Body/Body 2/body right side front.stp
Mechanicals/Body/Body 2/body side (1).obj
Mechanicals/Body/Body 2/body side (1).stp
Mechanicals/Body/Body 2/body side mirrored v3.obj
Mechanicals/Body/Body 2/body side mirrored v3.stp
Mechanicals/Body/Body 2/body side.obj
Mechanicals/Body/Body 2/body side.stp
Mechanicals/Body/Body 2/standard strut.obj
Mechanicals/Body/Body 2/wing attachment.obj
Mechanicals/Body/Body 2/wing attachment.stp
Mechanicals/Body/Body 2/x beam.obj
Mechanicals/Body/Body 2/x beam.stp
Mechanicals/Body/Body 3.1/body left side back.obj
Mechanicals/Body/Body 3.1/body left side back.stp
Mechanicals/Body/Body 3.1/body right side back.obj
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

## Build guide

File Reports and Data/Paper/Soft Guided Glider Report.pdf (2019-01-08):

# The Soft Guided Glider

Andrew C Brown
School of Engineering, Computing and Mathematics
Plymouth University
Plymouth, GB
andrew.brown-16@students.plymouth.ac.uk

Mark Q Campbell
School of Engineering, Computing and Mathematics
Plymouth University
Plymouth, GB
mark.campbell@students.plymouth.ac. uk

Connor Crabb-Thompson
School of Engineering, Computing and Mathematics
Plymouth University
Plymouth, GB
Connor.Crabb-Thompson@students.plymouth.ac.uk

Jeremy R May
School of Engineering, Computing and Mathematics
Plymouth University
Plymouth, GB
jeremy.may@students.plymouth.ac.uk

This document details the methodologies used to design and build a localizing glider which is capable of delivering vital supplies to people in need when they are in locations that are hard to reach by land.

Keywords—Glider, Soft Robotics, Compact, Compliant, Low cost, Lightweight,

I. INTRODUCTION
For this project various methodologies were used in order to design and build a soft, low cost glider with compliant wings. The compliant wings ensure that they don’t break when a collision occurs and allows them to be folded for the glider to be compactly stowed.

Much of the mechanical design was completed by using Computer Aided Design (CAD) and Computer Aided Manufacturing (CAM) software, and simulations were undertaken with the use of FEA (Finite Element Analysis).

Tensile testing was undertaken on different materials, including soft materials, to measure whether they were appropriate for use in the glider. Additional resources can be found concerning this glider on the GitHub repository [1].

II. MECHANICAL DESIGN
The mechanical design of the glider was undertaken with an iterative process, and each of the iterations were compared with the glide ratio.

The glide ratio is defined as the instantaneous ratio (https://www.yourdictionary.com/ratio) of rate of fall (https://www.yourdictionary.com/fall) to horizontal (https://www.yourdictionary.com/horizontal) speed (https://www.yourdictionary.com/speed) for a glider (https://www.yourdictionary.com/glider) [2]. In order to measure this, the height the glider was thrown from and the distance the glider moved was measured. The goal of the project was to design a glider with a glide ratio of 6:1 which is roughly half of a typical commercial glider.

A. Initial Design
The initial glider design was inspired by bats which have the ability to fold their wings, resulting in a very compact package.

The initial design therefore attempted to replicate the wing folding of bats, using the wing skeleton structure as a baseline. This skeleton was 3d printed in PLA and was wrapped in LDPE (a common plastic used to make bin bags) to form the skin. Online searches established the typical proportions of a glider providing an estimate of how big the wings should be compared with the body.

The first iteration was made with the purpose of developing an understanding of gliding. This concept model was cheap and made from lightweight materials that were easily accessible.

Upon testing, this concept model displayed:

- The importance of weight distribution
- When the wings were fixed in place, they were fragile

It was decided that each component part would be specifically designed. Both the strains to be imposed and the 3d printing orientation relative to the strain were considered in the design. In addition, crumple zones were included to improve the survivability of the glider upon impacts.

Further research established that whilst bats are very agile, they are very active flyers. As they do not spend much time gliding, the model of bat aerodynamics was not appropriate to the design objectives. Overall this version achieved a glide ratio of approximately 1:1.

After testing and analysing the bat glider design it was decided that a more traditional fixed wing design with much larger wings was required. To achieve the small storage volume and compliant wing, consideration was given to either wings that would fold up above the fuselage, or wings that would hinge to fold alongside the fuselage. It was decided that using hinges mounted on the body to fold the wings above the fuselage was the best solution. This would also allow use of existing model glider designs but with the acceptance that the glider would consume a larger overall volume than that of a bat design.

B. Wing Design
1) Prototype Wing Design

For the second iteration the wings were the primary focus. To prototype and test the aerofoil (wing profile), a sheet of

Figure 1 - An image of the 3D printed model of the wing aerofoil.

cardboard was folded around a CAD drawn model of the aerofoil (See Figure 1).

The cardboard wing was hollow with a wing span of 1.2m and a depth of 95mm. The aerofoil used for this prototype was the HS130, although it is hard to find data as to why this is a viable aerofoil it is a commonly used one for model gliders within the hobbyist space [3].

Once the wing was created a rudimentary body and tail was also made from cardboard and test flights were undertaken on this prototype glider (See Figure 2). For the cardboard prototype we found after a series of test flights its glider ratio was 2:1. It was decided that a lighter weight and larger surface area would allow a larger glide ratio along with a more refined design of body and tail.

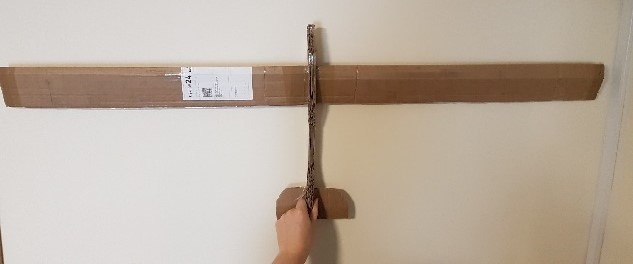
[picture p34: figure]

2) First Wing Design

To ensure that the wing was lightweight a skeletal structure was designed. In order to get the best balance between rigidity and weight, a test print was created (See Figure 3) with different thicknesses of the aerofoils. It was found that 1mm of thickness offered the best balance between weight and rigidity.

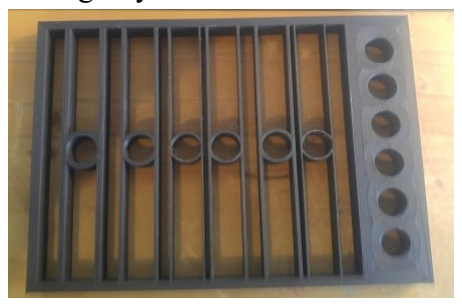
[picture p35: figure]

The further optimised aerofoils were printed and slid onto a PVC pipe so that the aerofoils were perpendicular to the pipe and evenly spaced. Next, 2 carbon fibre rods were glued to the leading and trailing edge on the aerofoils, and a lightweight shrink wrap material was stretched and glued around the wing, this material was later heated to shrink and tighten it further to the skeleton to leave a smooth surface.

The carbon fibre rods were added to:

- Add more rigidity to the wing and stop the aerofoils from becoming out of alignment
- Prevent the wrap from ‘drooping’ between the aerofoils when the heating element was applied.

To test the glider, the wing was initially designed to be fixed wing. However, it was designed so that the wing could be cut in half, when the folding mechanism was created.

The final dimensions of each wing were 390 x 145mm. Upon testing this wing configuration with a skeletal body as well, a glide ratio of 6:1 was achieved. A graph showing the results can be found on the GitHub repository [1].

3) Final Wing Design

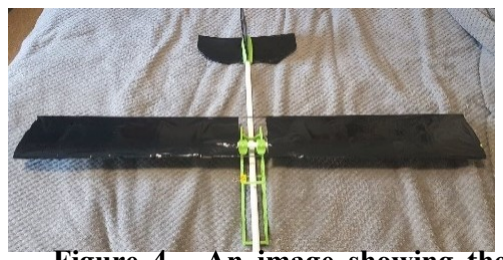
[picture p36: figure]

For the final revision of the wings, only slight adjustments were made.

- Each wing was made longer going from 390mm to 630mm (with no change in depth).
- The carbon fibre rod used on the trailing edge of the wing was replaced by a carbon fibre strip, this was to reduce the protrusion of the carbon fibre into the shape of the aerofoil.
- A different heating element was used to shrink the wrapping material moving from an iron on low heat to a heat gun. It was found that this gave a better more even finish on the wrapping material.

For this wing, simulations were undertaken to see the vertical displacement that would be produced by gravity between the mounting point of the wing to the tip of the wing. This value was calculated by hand and using FEA. For the FEA simulation it was found that there was a displacement of 1.149mm, a very small amount of vertical displacement when considering each wing is 630mm in length. The hand calculations were completed using the following equation:

Deflection under load =

WL

3
3EI
Where:
- W = the moment that is acting on the wing.
- L = the length of the beam.
- E = the young’s modulus of the PVC tube.
- I = the second moment of area of the PCV tube.

The moment acting on the wing was calculated by finding the centre of mass relative to the mounting point and the mass of the wing, both of which could be found from the simulated model in fusion 360. The moment was found using the following equation:
W = FD = 0.6047N ∗ 0.320m = 0.193504Nm

The Young’s modulus of PVC pipe was found to be 3.4GPa [4].

To find the deflection of the beam the second moment of area was used. As the PVC pipe was a hollow tube the following equation could be used:

INA =

π
4

(R

4 − r

4
)

Figure 4 - An image showing the fixed wing design.

Figure 2 - An image showing the cardboard glider prototype.

Figure 3 - The test piece used to find the optimum balance between rigidity and weight.

Where R is the outer diameter at 7mm and r is the inner diameter at 6mm. From these values, a second moment of area of 867.86m⁴ was found.

The length of the wing was 0.69m. With these values the deflection under load was calculated to be 4.96x10⁻⁶m. Although this number did not reflect that of the simulation, both numbers are sufficiently small enough to be negligible in the consideration of the wings. The difference is likely due to materials selections in fusion.

C. Body
1) Initial Body Design

Once the cardboard prototype and its testing were complete a body was designed in parallel with the first revision wings, this body was skeletal in structure having minimal internal support structure to allow internal space for electronics and the wing retraction mechanism. This allowed for lightweight design.

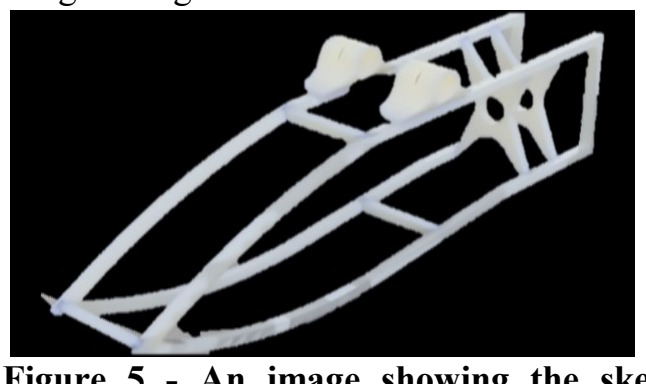
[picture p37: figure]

All the sections of the body were 3D printed and connected together using dove tail joints. A test piece was printed with different sizes and tolerances of dove tails to see which would give the best fit, this can be found in the GitHub Repository [1]. Once this was done the body was design printed and assembled.

This body was then tested with the wings as the first revision of the 3d printed glider. From testing this design it was clear that there were several issues with this design:

- There was not enough structure at the nose of the body leading to this being flimsy
- The point of the nose being so sharp meant that when the glider fell and landed nose first the body would shatter.
2) Secondary Body Design

For the next revision the body was altered in several ways:

- It was made more modular by increasing the number of pieces from 8 pieces to 16.
- The nose of the body was given more supports and was adjusted to be more rounded to better absorb impacts.

These adjustments resulted in a 6:1 glide ratio being achieved and less parts being broken. However, if a part was broken, it was removed easily, reprinted quickly, then reattached to allow testing to continue.

On this version some calculations were done to ensure that the body was balanced optimally for efficient flight [5]. The Static Margin (SM) was calculated to measure the stability of the plane. In order to find the SM, the Aerodynamic centre of the wing was calculated. This is the point where the force can be said to be exerted when the glider is being lifted. As the wings are rectangular, this was found easily as it fell 25% of wing length back from the leading edge, which was 37.5mm. The Aerodynamic centre of the tail was then found. The Aerodynamic centres were used to calculate the Neutral Point (NP). The NP is the centre of lift for the whole glider and was found using the following equation:

D = L ∗

tail area
tail area+wing area

Where:

- L is the distance between the aerodynamic centre of the tail and the wings.
- D is the distance the natural point is from the aerodynamic centre of the front wing.

It was calculated that the natural point of the glider was 69.28mm back from the aerodynamic centre of the wings.

Finally, the centre of gravity (CG) was found to be 56.78mm back from the leading edge of the wing. The glider is deemed to be stable in flight if the distance between the NP and the CG was ~10% of the Mean Aerodynamic Chord (MAC) which was found to be 145mm (the distance between the trailing and leading edge) [6]. This distance was found to be 12.42mm which is ~10% of the MAC. For this reason, it was concluded that the glider was optimally balanced.

3) Tertiary Body Design

For further iterations of the body design small changes were made to the structure to ensure that the centre of gravity was still positioned at the same point. Subsequent iterations had minor changes to improve structure such as:

- Increasing the size and material around crucial dove tail joints to make sure they did not break
- Changing the position of structural support pieces to allow for easier housing of the electronics along with reorientation of dovetail joints to make the body more rigid in all axis

For the final iteration, testing was undertaken to the nose piece using different combinations of Ninjaflex (a rubberised flexible material that can be 3D printed) and PLA. After comparing several combinations of these materials, it was found that using Ninjaflex support pieces along with PLA body pieces gave a good balance between malleability and rigidity, as when the glider impacted nose first the combination did not shatter, unlike an all PLA nose, but also absorbed the impact well and held its structure while in flight, unlike an all Ninjaflex nose. After these changes and minor iterations through testing, a final body design was produced.

D. Tail
The tail was once again designed as a skeletal structure and wrapped similarly to the wings to minimise weight. After researching it was found that there were 2 main tail designs intended to simplify control of the plane; the conventional tail and the T-tail [7]. The T-tail was designed with the purpose of getting the horizontal fin out of the prop wash and the wing wake. Seeing as a glider does not have an engine, the prop wash was not of concern. It was therefore decided that the

Figure 5 - An image showing the skeletal structure of the glider body.

simplified mounting of the conventional tail would be implemented for this glider as it allows a more skeletal design, resulting in reduced weight.

Research was then undertaken to establish the proportions of the fins. It was found that the surface area of the 2 horizontal fins together should be 25% the surface area of the wings and the vertical 50% of that [8], but the shape was not as important. Therefore, due to the size limitations of the 3d printer we were using, it was decided to make the fins square.

The horizontal fins were designed to be easily adapted to incorporate elevators to allow steering once the electronics had been incorporated. It was decided that elevators would be used for steering since the wing’s design would make it very hard to include flaps or ailerons. The secondary reason was that all the control we needed could be achieved through elevators while minimising the effort required to control the glider.

E. Wing Hinge
For this glider, a requirement was that it should be able to be stored compactly and for it to be compliant. In order to achieve this, the wings were designed to be placed on hinges at the body so that they could move from their flight position (perpendicular to the body) to parallel with the body.

For this design, considerations were made to ensure the wings were supported but would also be able to pivot. For this a system of two bearings were used to attach the body of the glider to each wing. From the bearing protruded a rod that had a mount for the wing to attach perpendicularly and grooves at the top and bottom. These grooves were used to attach bands between the two bearing rods, these bands would counter leaver each wing against each other and allow the wings to pivot smoothly. This meant detail would have to be put towards the bands to make sure they were strong enough to hold the wings. Figure 7 depicts this mechanical arrangement.

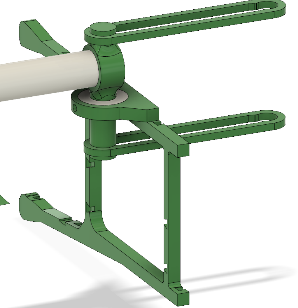
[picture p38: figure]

Finite Element Analysis (FEA) was done on the models to calculate several things:

The safety factor of the bearing mount was investigated initially without the support bands. If the value of the safety factor is less than 1, there is a guaranteed breakage. For this test, the minimum safety factor of 0.108 was collected, showing the necessity of the support bands.

The next two areas that were tested for their safety factor and displacement were the rod and the bands. For these tests a torque was found that would be produced by the wings due to gravity and these were applied to the two models in simulation. The safety factor for the rod and band where 4.491 and 8 respectively while the displacements were at maximum

0.16mm and 8.758E^-4mm respectively. These results showed that the wings would be supported by this mechanism.

Once the support for the separate wings was designed, the pivoting design was created, for this all that was needed was a bearing. Several different bearings were investigated, and a nylon bearing was chosen that ensured a lightweight design whilst still allowing for the wings to pivot.

The final attribute of the pivoting design was a stopper that stopped the wings from hyper extending past the perpendicular and moving in front of the glider body. This part was tested using FEA and a force that was calculated using the mass of the wing and the acceleration of the wing when it hit the stopper. The acceleration was found using an accelerometer attached to the wing, which detected the acceleration as the wing unfolded and hit the stopper. The safety factor was found to be 8+ and so the part was easily capable of preforming its role.

All of the finite element analysis reports can be found in the GitHub repository [1].

F. Retraction Mechanism
The glider was designed so that the wings would passively be in the gliding position due to the Filaflex elasticated material pulling the two wings together at the leading edge, where they were held against the stopper.

In order to retract the wings, an active system was designed by using a servo and gear train to spin a spool. This spool would then turn coil tethers connected to the trailing edge of each wing, in order to retract them.

The gearing was designed to have a point at the end of the retraction that would disconnect the driving gear from the spooling gear. This allows the spooling gear to unwind and uncoil the tethers that are in direct competition with the Filaflex material.

To drive this gearing a 180° 9-gram positional servo was used. From some simple calculations on where the tether would connect to the wing and that connection’s distance from the pivot point, it was found that the tether would have to coil in at least 141.37mm to fully retract the wings. This value was used to design the two gears.

For the driving gear there were a few restrictions to its design:

- It could only have 135° of teeth to drive the gear due to the release section of the gear needing the additional 45° to fully disconnect from the spool.
- The size of the glider itself causing the maximum radius the gear could be to 30mm otherwise the gear would protrude from the glider body.

With these restrictions, the driving gear was made to be 25mm in radius. The spool gear was designed by having the spool directly attached to a gear that would connect to the drive gear. It was found that the spool gear with a radius of 6mm and a spool with 15mm radius attached to the smaller gear would give enough rotation to retract the tethers fully. The calculations describing this and a model can be seen in the following equation:
Ratio of drive gear to spool gear = 4.16: 1

Figure 7 - An image showing the arrangement for the Wing Hinge.

This ratio indicates that for each degree the drive gear rotates the spool gear rotates 4.16 degrees. From this we can say that as there is only 135° of driving gear rotation that the spool gear will turn:

Rotation of spool gear = 135° * 4.16 = 561.6°

Knowing this we can look at the spool section of the spool gear and find that it has a circumference of:

C =2πr where r is 0.015m

C = 2π *0.015

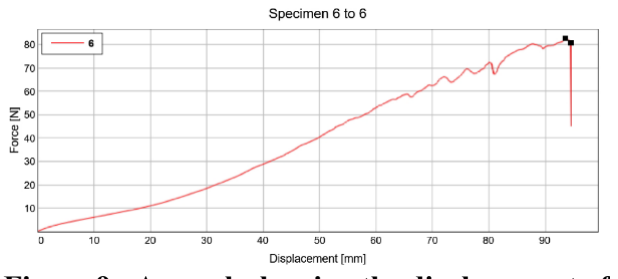
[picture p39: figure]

C = 0.0942m

We can then divide this number by 360 (a full rotation) to find the distance retracted by 1° then multiply it by 561.6 to find the total distance retracted.

0.0942 / 360 = 0.00026167m/deg

0.00026167*561.6 = 146.952mm

From these calculations we can see that the gearing system would retract the wings far enough for them to be fully folded. The gear system and its mount to the body can be seen in figure 8.

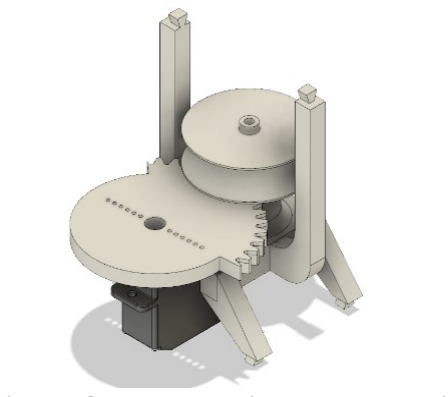
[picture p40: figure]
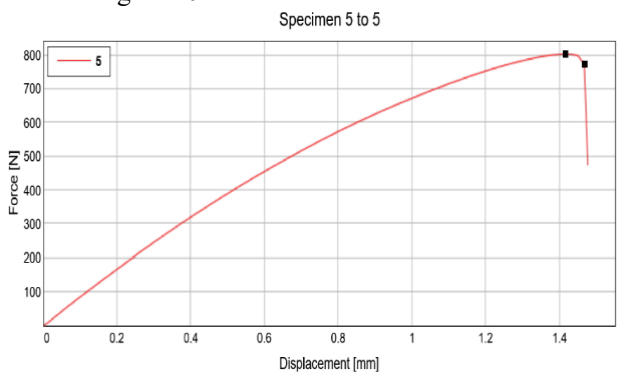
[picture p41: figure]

In theory this system would be able to coil the desired length of tether to retract the wing but when tested in practice it was found that the large torques needed to retract the wings could not be supplied by the servo. The main two reasons for this failure were:

- The rotational distance of the servo was increased on the gearing to provide enough rotation to coil the tether but this led to a decrease in torque applied to the coil meaning that less force could be used to pull the wings inwards.
- The wing was being pulled at a large angle from the parallel meaning that only a portion of the force was being applied from the tether to close the wings.

For these two reasons, the elastic force of the filaflex was not overcome and the wings were not retracted.

III. TENSILE TESTING
Tensile testing was undertaken to better understand the materials used and to see if they were suitable for their roles.

We started with the filaflex elasticated material that passively holds the wing in the gliding position. Through testing it was ensured that the material would not snap or plastically deform when used in the glider. Before testing the filaflex, other materials and mechanisms were investigated such as different springs and heavy duty (3mm thick) rubber bands. It was found that the springs would plastically deform due to the high extension they would have to endure. For the elastic band it was found that its elastic retraction force was not sufficient enough to hold the wings in place.

The filaflex was strong enough to hold the wings in position but did not hold them when initially thrown. To test the displacement capabilities of the material a tensile test was performed. 20mm of the material was used and the displacement of the material was measured with respect to the

force. The results can be seen in Figure 9.

The material was able to displace over 60mm before it began to deteriorate and eventually snap, it was found that this was also in the elastic region of the material. Due to the high extension of the filaflex, it was decided that this would be a useful material for the glider.

The next tensile test that was preformed was on the wing band. This was to test what force the band could take before plastically deforming or fracturing. The tensile test data can be seen in Figure 10.

This data shows that the band can hold a large force of 800N before plastically deforming and then later fracturing. This means the band is more than sufficient for use on the glider for supporting the wings.

Finally, the ninjaflex 3D print material was compared with PLA material. This was done by comparing the displacement of the gliders body strut that was present in both PLA and in Ninja flex. The the results for the tensile tests can be seen in Figure 11.

These graphs show that both materials have very different properties: Where the ninjaflex began plastically deforming after 100N of force it didn’t fracture until it was displaced by ~45mm. However, the PLA strut held a much larger force at

Figure 8 - The gearing system designed for the retraction mechanism.

Figure 9 - A graph showing the displacement of filaflex.

Figure 10 - A graph showing the displacement of the band over 1000N but then fractured very quickly afterwards as seen by the sharp fall in the graph.

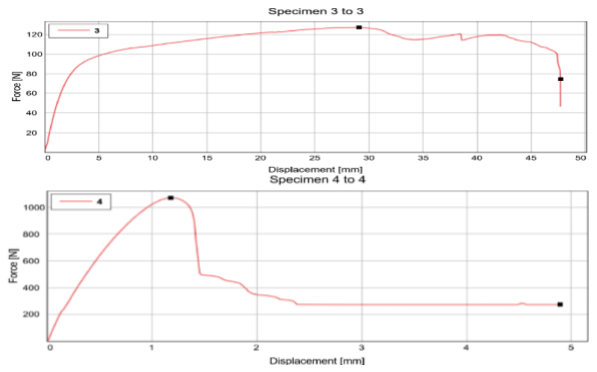
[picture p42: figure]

Other tensile tests were performed and can be seen on the GitHub repository [1].

IV. ELECTRICAL DESIGN
The electrical design focuses primarily on the stabilisation of the flight, localisation, steering and finally stalling the flight when the distance to the ground is low enough.
A. Power
In order to achieve electronic control, the power requirements were investigated.

Various batteries were considered for the use of powering the electronics. It was required that the battery was as light and compact as possible with enough charge for stabilised gliding for the duration of the glide. The battery used was the 200mAh 651723 battery due to its low weight, low cost and compactness. This battery outputs a voltage of 3.3V.

The LM2937 Voltage Regulator was used so that the 3.3V would be boosted to 5V, which would be sufficient to power the Arduino Nano and the servos. It was found that the voltage regulator did not successfully regulate the 3.3V to 5V, therefore, two 651723 batteries were placed in series to produce 6.6V. Due to the lightness and compactness, this did not have too negative an effect on the glider. This higher voltage was successfully regulated to 5V to power the Arduino nano and the servos.

Testing the battery life consisted of running the system with two servo constantly moving for the entirety of the test, this was achieved by editing the sweep.cpp programme provided by Arduino. Whilst running this code, the batteries lasted for an average of 1 hour 5 minutes and 16 seconds when run five times. This time is deemed to be the worst-case scenario for the gliding time. The data can be found on the GitHub repository [1].

B. Wing release mechanism
A requirement of the system was that the wings would spread out when the glider was initially dropped. This was achieved by taking regular readings with an accelerometer and measuring the difference between the readings. For the purposes of this, only the magnitude of the accelerometer readings was required which was collected using Pythagoras’ theorem:

Magnitude of acceleration = √X² + Y² + Z
2

In this equation, the X, Y and Z components represent the three directional readings from the accelerometer.

The wing was released when the difference between the current magnitude and the previous reading was greater than
0.4. The code implemented, and a demonstration video can be found on the GitHub repository [1].
C. Stabilisation
1) Accelerometer Testing

The Accelerometer was a useful tool for detecting sudden movements which would allow the wings to be deployed when the glider is initially dropped or thrown. The uses of the accelerometer were also investigated to see whether it could detect the roll, pitch and yaw.

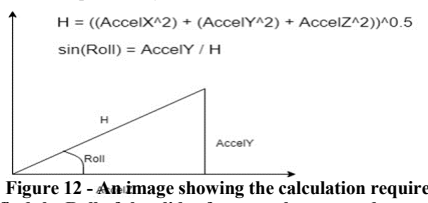
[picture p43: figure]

By applying the equations found in Figure 12, it was found that the roll, pitch and yaw could be calculated with respect to the Earth’s surface. From further research it was found that this is only effective when there is no acceleration except for the acceleration due to gravity [8]. For this reason, the gyroscope was researched.

2) Gyroscope Testing

The Gyroscope naturally measures the angular velocity in the X, Y and Z axis. These velocity values were integrated in order to approximate the angular displacement. With this methodology, the angular displacement calculation was not dependent on being without acceleration. However, because a continuous integration was not possible, there was a drift in the system.

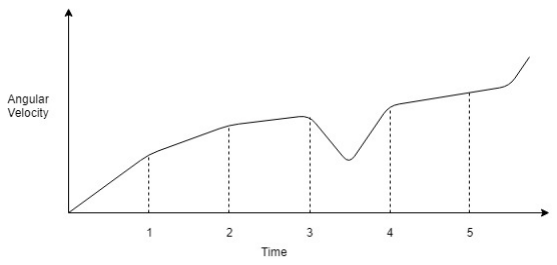
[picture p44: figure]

The drift is caused by not having a high enough frequency to detect all the changes in velocity. As can be seen in Figure 13, between T=3 and T=4 there is a dip in velocity, however this would not be detected. It is these missed changes in velocity that cause drift. This drift can be minimised by maximising the frequency at which the readings of the sensor are taken.

Angular Displacement = ∫ Angular Velocity dt

t

0

≈ ∑Angular Velocity ∗ Ts

t

0

Figure 12 - An image showing the calculation required to find the Roll of the glider from accelerometer data.

Figure 13 - A graph showing the time intervals for measuring the angular velocity from the gyroscope.

Figure 11 - A pair of graphs showing the comparison between Ninjaflex (specimen 3) and PLA (specimen 4)

From these investigations, the use of the accelerometer and gyroscope together was investigated.

3) Stabilisation with Accelerometer and Gyroscope data

In order to minimise the effect of the drift of the Gyroscope, a complimentary filter was used between the Gyroscope and the Accelerometer.

With this complimentary filter, the drift from the Gyroscope was negated. However, it was recorded that if the frequency became too low, so that the drift returned, the complimentary filter would be adjusted to give more weighting to the accelerometer reading to negate it once more.

Upon proving this method with a separate gyroscope and accelerometer, the circuitry size was minimised by using the MPU6050 that incorporates the accelerometer and gyroscope together for this exact purpose, and the accompanying library was used that is fully optimised for the MPU6050 and uses the same method that was proven and tested.

4) PID Control

The PID was later introduced so that greater control would be accomplished. For the PID to work, the required angle from the pitch and roll was initially set to 0, however, this value would later be changed to a different value in order to steer the glider. To tune the system, the proportional value was initially set to two as the servo output would be taking only half of the input due to the complimentary filter between the roll and pitch.

In order to protect the servos, the maximum and minimum values of the output were set so that if the final PID value became too large, the servos would not be sent to an angle that exceeded their limit and caused them damage.

The differential part of the PID was next to be set which took into account the rate of growth of the error and acted to negate it. Finally, the integral part was tuned so that any residual error is minimised, and any correction is completed smoothly without jitter.

From the output of the PID, the servos were programmed to move against the roll or pitch. This was achieved by using a complimentary filter with the two inputs.

Rigℎt Servo Output = (Roll Value ∗ 0.5) − (Pitcℎ Value ∗ 0.5) + 90

Left Servo Output = (Roll Value ∗ 0.5) + (Pitcℎ Value ∗ 0.5) + 90

The Pitch is inverted for the right servo instead of the roll, due to the fact that the servos are placed on the opposite sides of the plane and facing in opposite directions. The code implemented, and a demonstration video can be found on the GitHub repository [1].

D. Localisation & Steering Research
To be able to turn the glider from an actively stabilising glider into an autonomous glider that could safely travel to a specific position, some extra sensors for finding the glider’s position relative to other objects were necessary.
1) GPS

The purpose of the GPS sensor was to localise the glider to a global position in order to calculate the required direction of travel for the glider to reach the target location.

The Adafruit 746 GPS module [10] was selected due to it being affordable and a well-supported module that came with example code which could be used to test the GPS tracking and would be easily integrated into the glider.

The GPS module was tested to see what information was provided and investigations took place to understand how to implement it into the glider design. The code started up the GPS satellite tracking of the module and waited to get a fix on its location. When the location fix was achieved, the longitudinal and latitudinal position of the module, along with the direction in which it was travelling, and the current GMT were provided.

From the code provided, elements could be altered in order to obtain the module’s position and direction of travel. Once this data was collected, the next step was to establish a target position for the glider to reach; by comparing the glider’s original position and direction relative to the desired target position, a vector was calculated. This vector acted as a guide for the glider and would allow for its flight course to be altered in the direction of the target position. The equation for this can be seen below as Direction angle.

Direction angle = tan(

Target Longitude − Current Longitude Target Latitude − Current Latitude )

The vector informed the glider if it was heading in the correct direction and which way it needed to turn in order to face the correct direction and ultimately reach the target position.

Once this information was obtained the direction that the glider needed to turn would be fed to the PID, which would bank and turn until the GPS sensed it was facing the right direction. At this point, the glider would stop banking and level itself off and head straight.

Although this type of localisation provides a reference of where the glider is relative to the earth and can help with direction of travel to a target position, it will struggle to deal with obstacles in the glider’s direct vicinity that may need to be avoided. It will also not be able to calculate the height of the glider from the ground and would thus fail to stall for landing.

2) Close-Proximity Sensors

It was considered that the glider should detect obstacles and avoid them by banking. Additionally, in order to land smoothly by stalling the flight, the distance to the ground needed to be considered. In order to achieve this, Close-Proximity sensors were investigated.

These close-proximity sensors would be fixed to the front and bottom of the glider in order to detect any approaching obstacles from the front and to calculate the distance to the ground.

a) Ultrasound sensors
The HC-SR04 [11] and the SRF05 [12] ultrasonic range finders were investigated for this, due to both being relatively easy to use, the former being very cheap (≈60p each) and the latter having a high working range.

Once the distance was calculated, the sensors could be calibrated to adjust the accuracy of the distance measured by setting the sensors at a set distance from an object and calculating the error at each set distance. An equation could

(Gyro Angle ∗ 0.98) + (Accelerometer Angle ∗ 0.02) = Rotation Angle then be formulated to adjust the sensor readings to increase the accuracy of the readings.

If the sensors detected an object within a threshold distance of the front of the glider, a new required angle would be sent to the PID telling it to turn away before collision.

When the sensor underneath the glider detected that it was within close proximity to an object, it would assume this object was the ground and would prepare for landing. At this point, the glider would get the PID to try and stall the glider by pulling up and then folding in its wings, so it could ensure a safer landing.

The problem with using an ultrasound sensor is that it can easily pick up refractions off to one side of the glider and interpret these responses as objects being closer than they are.

b) Infra-red Sensors
The infrared (IR) sensor was also investigated, that used light instead of sound to calculate distance to other objects. The IR Sensor emits light towards an object in a single line rather than a cone, and the intensity of the light bounced back will affect the analogue voltage on the IR sensor module. This analogue reading is then calibrated, similarly to the ultrasound method, to calculate the distance.
c) Evaluation of Close-Priximity Sensors
While IR sensors are typically cheaper than the ultrasound sensors, they do not usually detect the same distances unless more expensive sensors are used.

While the ultrasound sensor picks up some false distances from refraction, the IR sensor will not, but it can instead pick up some parts of the visible spectrum as false distances and make it difficult to calibrate distances.

Due to IR distance sensors normally operating under 1 metre and the HC-SR04 ultrasound sensor having an operational range of approximately 0.5 metres, the optimal sensor, which was ultimately selected for this project, was the SRF05 Ultrasonic range finder, with its superior operational range of 4 metres.

V. INTEGRATING ELECTRONICS INTO MECHANICAL DESIGN
For the final revision of the glider, the stabilisation electronics were incorporated into the mechanical design. This involved creating a mount for both the servos and the electronic circuitry. This was done with ease as an area had already been allocated for this purpose in the previous versions. The servos that controlled the tail fins were placed in the body and controlled the back elevators via metal rods which would push and pull the tail flaps to steer the glider.

The tail fins were designed with a connector for the metal rod so that when they were pushed or pulled it would pivot the fins in the desired direction.

VI. CONCLUSION AND FURTHER DEVELOPMENT
The development of the glider proved to be successful, achieving a 6:1 glide ratio. However, the retraction mechanism and compliant wing design was less successful; Although time and consideration had been put into the design, not all real-world factors were considered, such as the force exterted on the wings when initially thrown.

Given more time, the areas in which further development would be undertaken would be in:

- Implementing the localisation and steering research into the glider design
- Implementing an Agonist-Antagonist joint for the retraction and compliancy of the wings instead of the active-passive arrangement.

The Agonist-Antagonist joint would adjust the stiffness and the orientation of the wings with respect to the body with the use of two motorised pulleys, mounted on the fuselage. If the front pulley was coiled up, then it would pull the wings forwards and if the back pulley was coiled up, then it would pull the wings back. If both pulley’s tightened then the wings would become stiffer and if they loosened, the wings would become more compliant. The designs for this can be found on the GitHub repository [1].

VII. ACKNOWLEDGMENT
Thanks must be made to Martin Stoelen and the technical staff who assisted with the development of the glider.

VIII.REFERENCES

[1] Brown, A., Crabb-Thompson, C., May, J. and Campbell, M.
(2019). markcampbell102/Soft-Guided-Glider. | [online] | GitHub.
Available | at: | https://github.com/markcampbell102/Soft-Guided-
Glider (https://github.com/markcampbell102/Soft-Guided-Glider) [Accessed 7 Jan. 2019].
[2] Yourdictionary.com. (2019). Glide-ratio dictionary definition | glide-
ratio | defined. | [online] | Available | at:
https://www.yourdictionary.com/glide-ratio [Accessed 2 Jan. 2019].
[3] Siegmann, H. (2019). Airfoil Database for Tailless and Flying Wings.
[online] | | Aerodesign.de. | | | Available | at:
http://www.aerodesign.de/english/profile/profile_s.htm#hs130 [Accessed 2 Jan. 2019].
[4] En.wikipedia.org. (2019). Polyvinyl chloride. [online] Available at: https://en.wikipedia.org/wiki/Polyvinyl_chloride [Accessed 2 Jan. 2019].
[5] Instructables.com. (2019). Easy Aircraft Design. [online] Available at: https://www.instructables.com/id/Introduction-65/?fbclid=IwAR3DTwQWuHbQ_dBJY5pEUV2ls-
zcKe1yxXj_9Yp1WJoBY7UWp8e7pGaB7V0 (https://www.instructables.com/id/Introduction-65/) | [Accessed | 2 | Jan.
2019].
[6] Skybrary.aero. (2019). Mean Aerodynamic Chord (MAC) - SKYbrary
Aviation | Safety. | [online] | Available | at:
https://www.skybrary.aero/index.php/Mean_Aerodynamic_Chord_(M AC) (https://www.skybrary.aero/index.php/Mean_Aerodynamic_Chord_(MAC)) [Accessed 2 Jan. 2019].
[7] What-when-how.com. (2019). Tail designs. [online] Available at: http://what-when-how.com/flight/tail-designs/?fbclid=IwAR1GBtm9i9JqYvmVBX8s27GZv9Fo6yk9Ln42 y-ZsrViXJtx5bHuc6agkgJs (http://what-when-how.com/flight/tail-designs/) [Accessed 1 Jan. 2019].
[8] Students.iitk.ac.in. | (2019). | [online] | Available | at:
http://students.iitk.ac.in/aeromodelling/downloads/glider.pdf?fbclid=I wAR16mBGuHHNZ8wiMHxd7dQzh-tU_mOlzMdXLjdQ6Uuw3Kiw7sNnpxw_SPPo (http://students.iitk.ac.in/aeromodelling/downloads/glider.pdf) [Accessed 2 Jan. 2019].
[9] Goodrich, R. (2018). Accelerometer vs. Gyroscope: What's the
Difference? | [online] | Live | Science. | Available | at:
https://www.livescience.com/40103-accelerometer-vs-gyroscope.html [Accessed 1 Jan 2019].
[10] RS, 2019. ADAFRUIT INDUSTRIES 746 GPS Module. [Online]
Available | at: | https://uk.rs-online.com/web/p/gps-chips-gps-
modules/9054630/ (https://uk.rs-online.com/web/p/gps-chips-gps-modules/9054630/) [Accessed 1 Jan 2019].
[11] Sparkfun, | 2019. | Ultrasonic | Sensor | - | HC-SR04. | [Online]
Available at: https://www.sparkfun.com/products/13959 [Accessed 10 2018].
[12] Rapid, 2019. Devantech SRF05 Ultrasonic Range Finder. [Online]
Available | at: | https://www.rapidonline.com/devantech-srf05-
ultrasonic-range-finder-78-1085 (https://www.rapidonline.com/devantech-srf05-ultrasonic-range-finder-78-1085) [Accessed 1 Jan 2019

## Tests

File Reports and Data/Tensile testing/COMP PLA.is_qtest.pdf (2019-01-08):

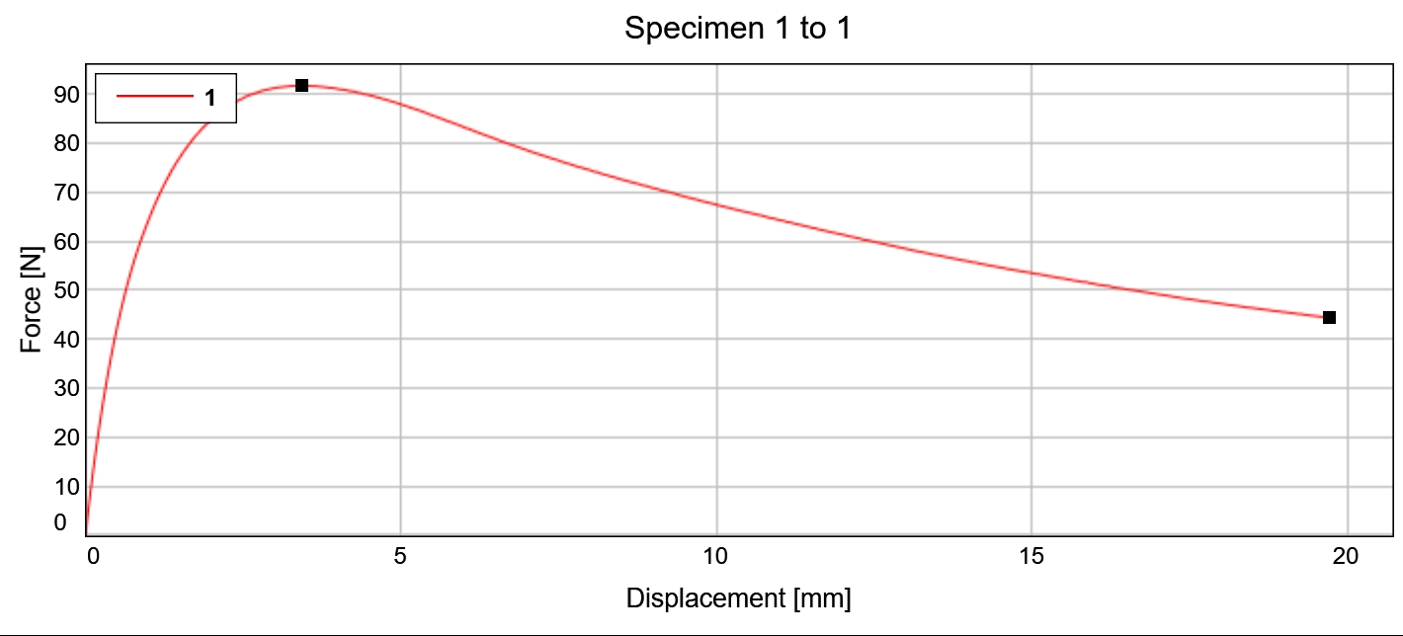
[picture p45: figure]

| Maximum Force [kN] | Displacement at Maximum Force [mm] | Maximum Displacement [mm] | Force at Break (Standard) [kN]
1 | 0.09 | 3.43 | 19.75 | 0.04

Specimen text input
COMPRESSION PLA 101MM START 1

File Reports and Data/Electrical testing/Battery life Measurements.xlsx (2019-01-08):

2 Servo's running on sweep (Starting from fully charged)
Attempt | Time
1 | 1:04:45
2 | 1:05:16
3 | 1:05:18
4 | 1:08:18
5 | 1:02:44
Average | 1:05:16
Range | 0:05:34
 | 8.53%

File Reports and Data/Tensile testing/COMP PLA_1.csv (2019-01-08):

Results Table 1
 | Maximum Force | Displacement at Maximum Force | Maximum Displacement | Force at Break (Standard) | Specimen text input
 | (kN) | (mm) | (mm) | (kN)
1 | 0.09 | 3.43 | 19.75 | 0.04 | COMPRESSION PLA 101MM START
Results Table 2

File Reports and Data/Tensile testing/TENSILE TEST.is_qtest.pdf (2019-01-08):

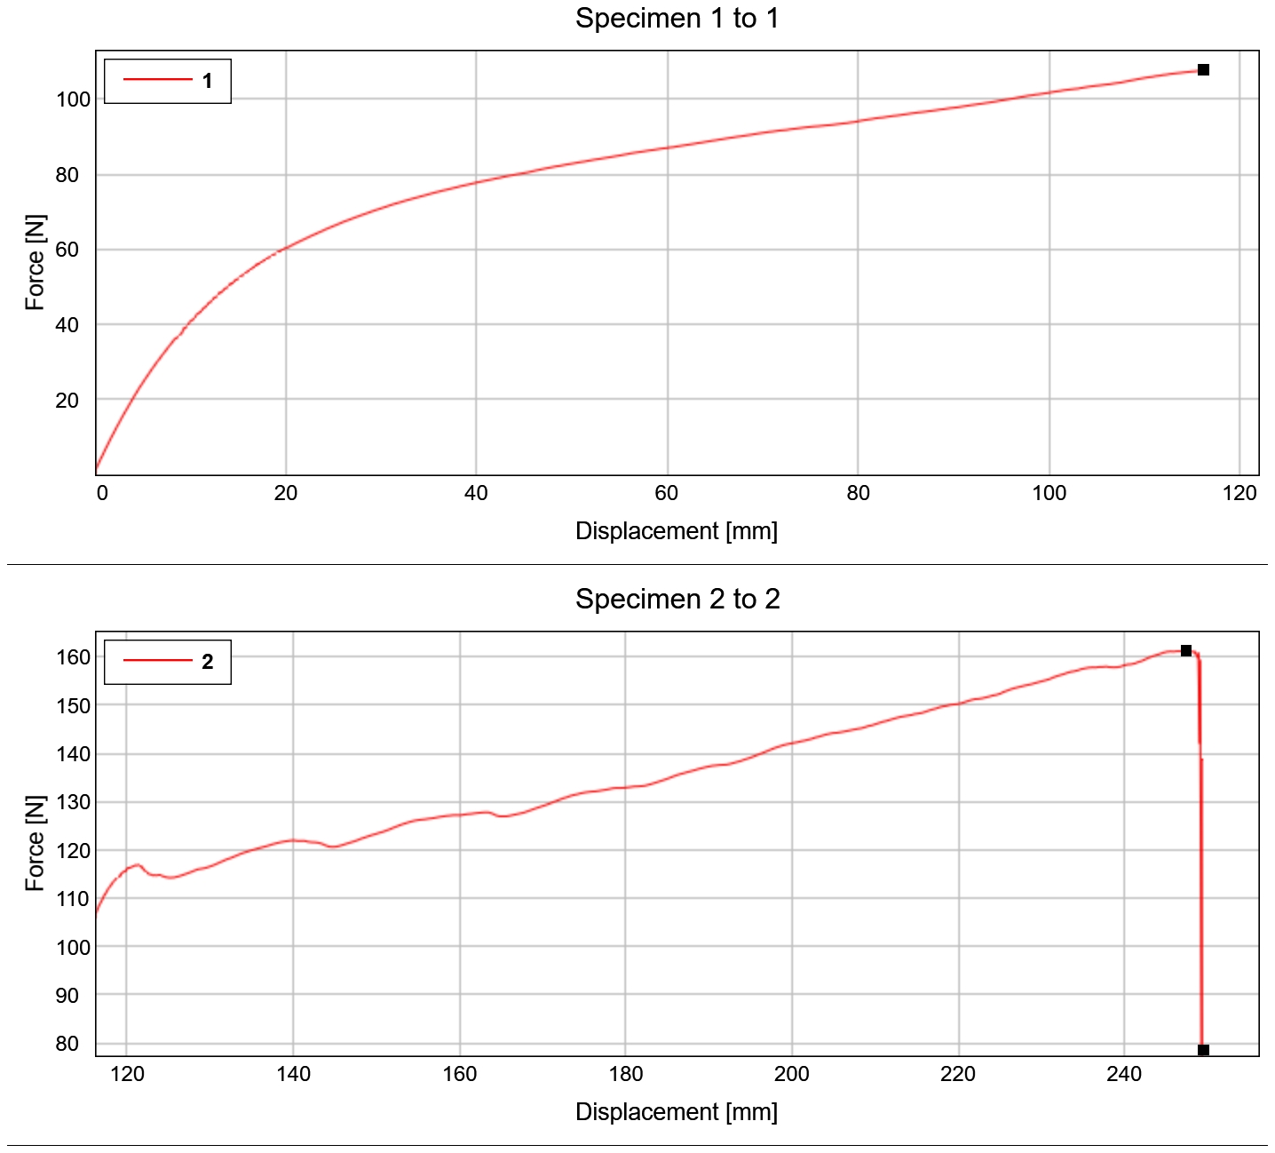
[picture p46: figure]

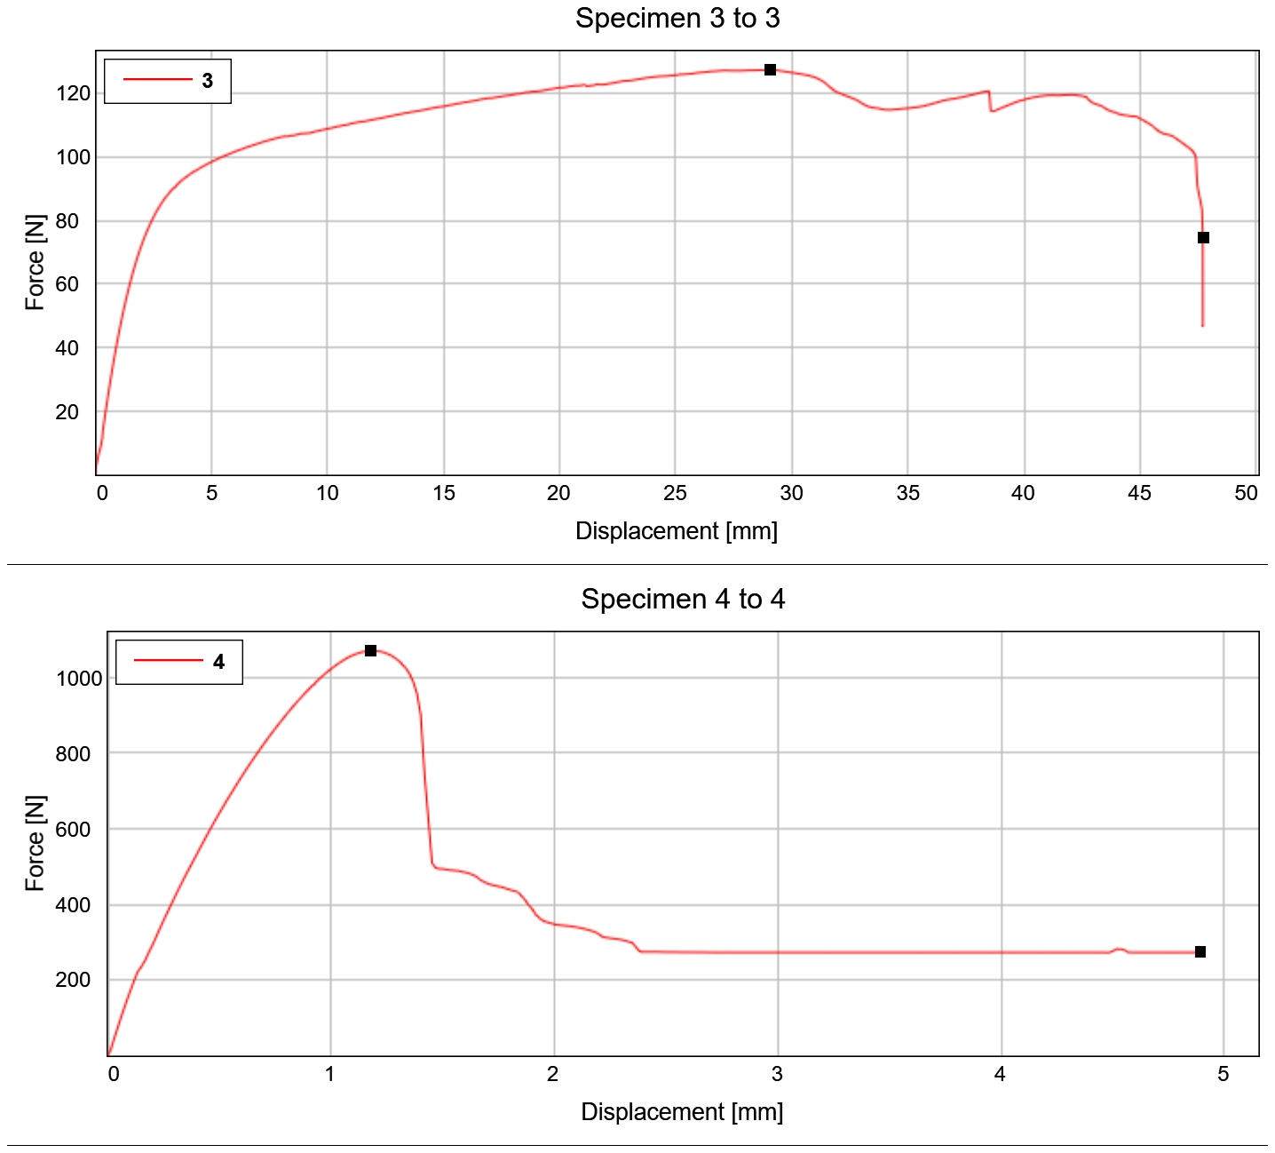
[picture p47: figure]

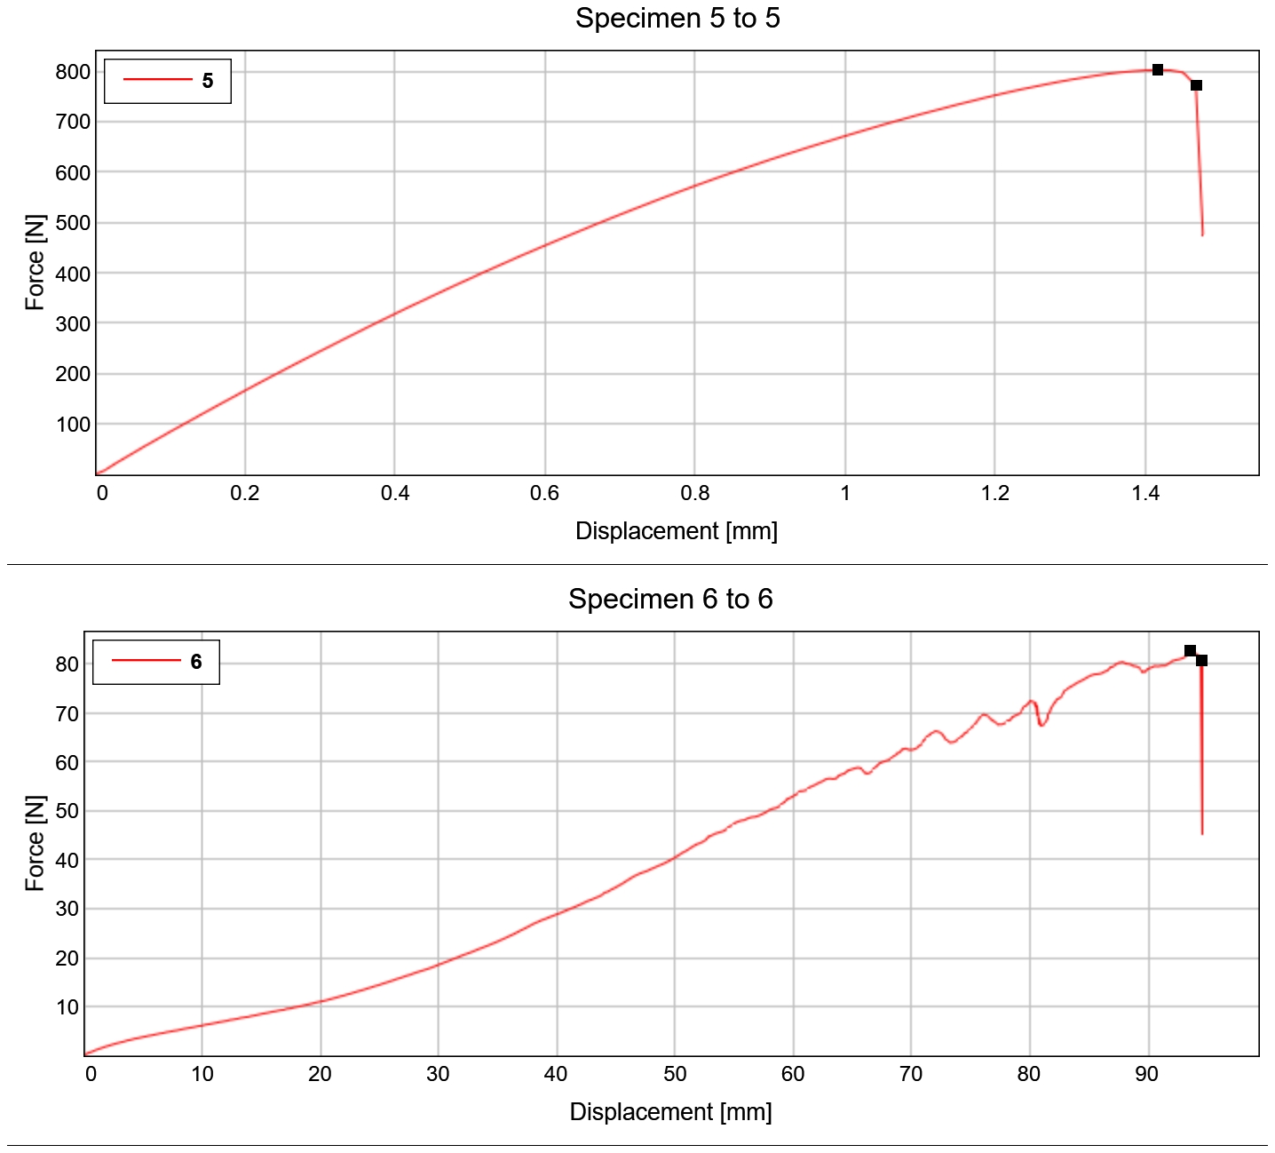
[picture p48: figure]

| Maximum Force [kN] | Displacement at Maximum Force [mm] | Maximum Displacement [mm] | Force at Break (Standard) [kN]
1 | 0.11 | 116.14 | 116.17 | 0.11
2 | 0.16 | 247.44 | 249.37 | 0.08
3 | 0.13 | 29.03 | 47.71 | 0.07
4 | 1.07 | 1.18 | 4.91 | 0.27
5 | 0.80 | 1.42 | 1.48 | 0.77
6 | 0.08 | 93.67 | 94.63 | 0.08
| Specimen text input
1 | FRONT BODY 1

| Specimen text input
2 | fRONT BODY 2
3 | STRUT NINJA FLEX
4 | STRUT PLA
5 | WING BAND
6 | FILAFLEX

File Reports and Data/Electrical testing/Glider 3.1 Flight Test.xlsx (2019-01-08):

Test Number | Initial Vertical Height / m | Horizontal Distance Travelled / m | Landing Height / m | Glide Ratio | Max Error | Min Error | Average Glide Ratio | Average Glide Ratio exclusing fail throws
1 | 1.7 | 3.7 | 0 | 2.18 | 3.699351238 | 0.6535899384 | 6.09 | 6.59
2 | 1.7 | 5.2 | 0.7 | 5.20 | 6.72288065 | 3.67711935
3 | 1.7 | 5.2 | 0.9 | 6.50 | 8.02288065 | 4.97711935
4 | 1.7 | 6 | 0.75 | 6.32 | 7.838670124 | 4.792908824
5 | 1.7 | 6.5 | 0.9 | 8.12 | 9.64788065 | 6.60211935
6 | 1.7 | 5.8 | 0.7 | 5.80 | 7.32288065 | 4.27711935
7 | 1.7 | 4.9 | 0.9 | 6.13 | 7.64788065 | 4.60211935
8 | 1.7 | 6.5 | 0.7 | 6.50 | 8.02288065 | 4.97711935
9 | 1.7 | 5.8 | 0.7 | 5.80 | 7.32288065 | 4.27711935
10 | 1.7 | 5.8 | 0.4 | 4.46 | 5.984419111 | 2.938657812
11 | 1.7 | 5.8 | 0.7 | 5.80 | 7.32288065 | 4.27711935
12 | 1.7 | 6.5 | 0.9 | 8.12 | 9.64788065 | 6.60211935
13 | 1.7 | 6.5 | 0.9 | 8.12 | 9.64788065 | 6.60211935
14 | 1.7 | 4.2 | 0 | 2.47 | 3.993468885 | 0.9477075854
15 | 1.7 | 5.2 | 0.75 | 5.47 | 6.99656486 | 3.950803561
16 | 1.7 | 5.2 | 0.9 | 6.50 | 8.02288065 | 4.97711935
17 | 1.7 | 5.2 | 0.7 | 5.20 | 6.72288065 | 3.67711935
18 | 1.7 | 6.5 | 0.9 | 8.12 | 9.64788065 | 6.60211935
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

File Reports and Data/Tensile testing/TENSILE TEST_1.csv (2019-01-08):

Results Table 1
 | Maximum Force | Displacement at Maximum Force | Maximum Displacement | Force at Break (Standard) | Specimen text input
 | (kN) | (mm) | (mm) | (kN)
1 | 0.11 | 116.14 | 116.17 | 0.11 | FRONT BODY 1
2 | 0.16 | 247.44 | 249.37 | 0.08 | fRONT BODY 2
3 | 0.13 | 29.03 | 47.71 | 0.07 | STRUT NINJA FLEX
4 | 1.07 | 1.18 | 4.91 | 0.27 | STRUT PLA
5 | 0.80 | 1.42 | 1.48 | 0.77 | WING BAND
6 | 0.08 | 93.67 | 94.63 | 0.08 | FILAFLEX
Results Table 2

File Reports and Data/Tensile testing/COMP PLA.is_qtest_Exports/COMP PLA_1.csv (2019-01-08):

Time | Displacement | Force
(s) | (mm) | (kN)
0.0000 | 0.0000 | -0.0001
0.1000 | 0.0036 | 0.0001
0.2000 | 0.0137 | 0.0012
0.3000 | 0.0233 | 0.0024
0.4000 | 0.0324 | 0.0034
0.5000 | 0.0412 | 0.0044
0.6000 | 0.0496 | 0.0054
0.7000 | 0.0583 | 0.0063
0.8000 | 0.0668 | 0.0072
0.9000 | 0.0751 | 0.0081
1.0000 | 0.0835 | 0.0090
1.1000 | 0.0923 | 0.0099
1.2000 | 0.1003 | 0.0107
1.3000 | 0.1087 | 0.0116
1.4000 | 0.1173 | 0.0124
1.5000 | 0.1253 | 0.0133
1.6000 | 0.1335 | 0.0140
1.7000 | 0.1419 | 0.0149
1.8000 | 0.1503 | 0.0157
1.9000 | 0.1583 | 0.0164
2.0000 | 0.1667 | 0.0172
2.1000 | 0.1752 | 0.0180
2.2000 | 0.1835 | 0.0187
2.3000 | 0.1917 | 0.0195
2.4000 | 0.2001 | 0.0203
2.5000 | 0.2087 | 0.0210
2.6000 | 0.2169 | 0.0217
2.7000 | 0.2253 | 0.0225
2.8000 | 0.2339 | 0.0232
2.9000 | 0.2421 | 0.0239
3.0000 | 0.2504 | 0.0246
3.1000 | 0.2587 | 0.0253
3.2000 | 0.2672 | 0.0260
3.3000 | 0.2752 | 0.0267
3.4000 | 0.2835 | 0.0273
3.5000 | 0.2917 | 0.0279
3.6000 | 0.3001 | 0.0286
3.7000 | 0.3084 | 0.0292
3.8000 | 0.3167 | 0.0298
3.9000 | 0.3252 | 0.0305
4.0000 | 0.3335 | 0.0311
4.1000 | 0.3419 | 0.0317
4.2000 | 0.3504 | 0.0323
4.3000 | 0.3588 | 0.0330
4.4000 | 0.3672 | 0.0335
4.5000 | 0.3753 | 0.0341
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

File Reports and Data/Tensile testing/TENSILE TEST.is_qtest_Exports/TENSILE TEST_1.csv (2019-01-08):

Time | Displacement | Force
(s) | (mm) | (kN)
0.0000 | 0.0000 | 0.0000
0.1000 | 0.0039 | 0.0000
0.2000 | 0.0137 | 0.0001
0.3000 | 0.0233 | 0.0001
0.4000 | 0.0325 | 0.0002
0.5000 | 0.0412 | 0.0002
0.6000 | 0.0496 | 0.0003
0.7000 | 0.0583 | 0.0005
0.8000 | 0.0665 | 0.0003
0.9000 | 0.0749 | 0.0004
1.0000 | 0.0835 | 0.0004
1.1000 | 0.0919 | 0.0006
1.2000 | 0.1003 | 0.0006
1.3000 | 0.1088 | 0.0007
1.4000 | 0.1172 | 0.0006
1.5000 | 0.1253 | 0.0007
1.6000 | 0.1336 | 0.0007
1.7000 | 0.1419 | 0.0009
1.8000 | 0.1503 | 0.0008
1.9000 | 0.1584 | 0.0009
2.0000 | 0.1665 | 0.0009
2.1000 | 0.1752 | 0.0010
2.2000 | 0.1833 | 0.0010
2.3000 | 0.1915 | 0.0011
2.4000 | 0.1999 | 0.0011
2.5000 | 0.2085 | 0.0012
2.6000 | 0.2167 | 0.0012
2.7000 | 0.2252 | 0.0013
2.8000 | 0.2337 | 0.0013
2.9000 | 0.2420 | 0.0013
3.0000 | 0.2505 | 0.0013
3.1000 | 0.2587 | 0.0014
3.2000 | 0.2671 | 0.0015
3.3000 | 0.2753 | 0.0015
3.4000 | 0.2835 | 0.0016
3.5000 | 0.2917 | 0.0016
3.6000 | 0.3003 | 0.0017
3.7000 | 0.3084 | 0.0017
3.8000 | 0.3165 | 0.0017
3.9000 | 0.3251 | 0.0018
4.0000 | 0.3333 | 0.0018
4.1000 | 0.3416 | 0.0019
4.2000 | 0.3500 | 0.0020
4.3000 | 0.3587 | 0.0020
4.4000 | 0.3668 | 0.0020
4.5000 | 0.3752 | 0.0021
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

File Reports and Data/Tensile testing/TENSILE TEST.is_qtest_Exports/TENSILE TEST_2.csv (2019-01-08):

Time | Displacement | Force
(s) | (mm) | (kN)
0.0000 | 116.1694 | 0.1058
0.1000 | 116.1920 | 0.1058
0.2000 | 116.2300 | 0.1060
0.3000 | 116.2667 | 0.1062
0.4000 | 116.3016 | 0.1063
0.5000 | 116.3353 | 0.1065
0.6000 | 116.3693 | 0.1066
0.7000 | 116.4035 | 0.1068
0.8000 | 116.4365 | 0.1070
0.9000 | 116.4696 | 0.1071
1.0000 | 116.5033 | 0.1072
1.1000 | 116.5372 | 0.1074
1.2000 | 116.5701 | 0.1075
1.3000 | 116.6031 | 0.1076
1.4000 | 116.6367 | 0.1078
1.5000 | 116.6704 | 0.1079
1.6000 | 116.7035 | 0.1080
1.7000 | 116.7364 | 0.1081
1.8000 | 116.7699 | 0.1082
1.9000 | 116.8037 | 0.1084
2.0000 | 116.8368 | 0.1085
2.1000 | 116.8696 | 0.1087
2.2000 | 116.9032 | 0.1087
2.3000 | 116.9372 | 0.1089
2.4000 | 116.9700 | 0.1090
2.5000 | 117.0031 | 0.1091
2.6000 | 117.0368 | 0.1092
2.7000 | 117.0705 | 0.1093
2.8000 | 117.1034 | 0.1094
2.9000 | 117.1364 | 0.1095
3.0000 | 117.1700 | 0.1096
3.1000 | 117.2036 | 0.1098
3.2000 | 117.2366 | 0.1099
3.3000 | 117.2697 | 0.1100
3.4000 | 117.3032 | 0.1101
3.5000 | 117.3371 | 0.1102
3.6000 | 117.3701 | 0.1103
3.7000 | 117.4031 | 0.1104
3.8000 | 117.4365 | 0.1105
3.9000 | 117.4704 | 0.1106
4.0000 | 117.5033 | 0.1107
4.1000 | 117.5364 | 0.1108
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

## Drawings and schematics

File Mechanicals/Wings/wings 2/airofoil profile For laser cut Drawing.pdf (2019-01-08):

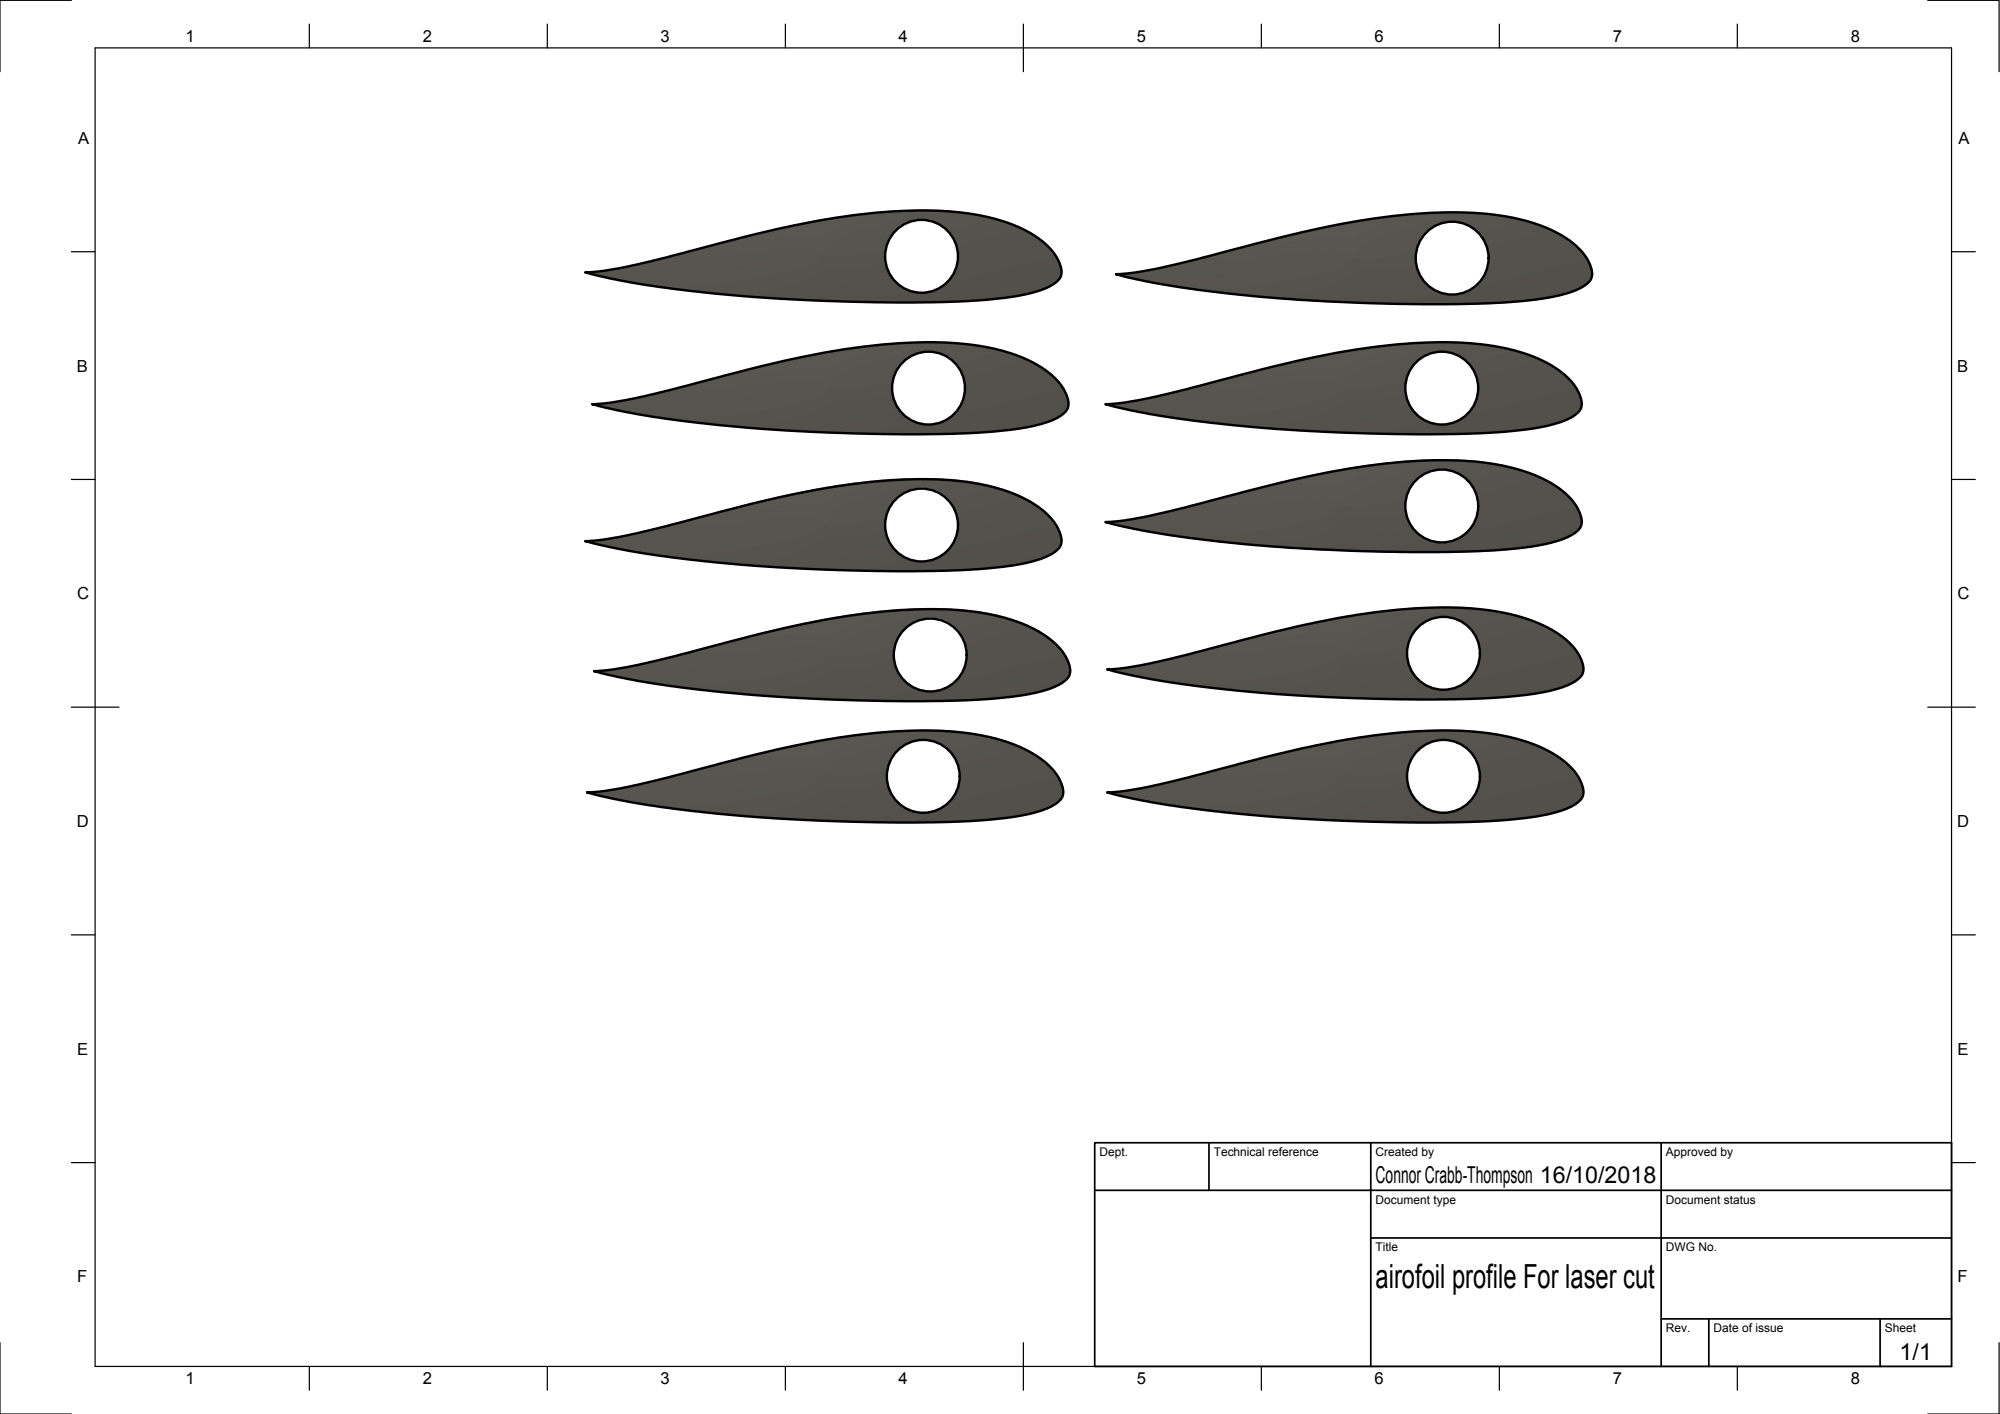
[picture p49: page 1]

Dept. | Technical reference | Created by Connor Crabb-Thompson 16/10/2018 | Approved by

Document type | Document status

Title airofoil profile For laser cut | DWG No.

Rev. | Date of issue | Sheet 1/1

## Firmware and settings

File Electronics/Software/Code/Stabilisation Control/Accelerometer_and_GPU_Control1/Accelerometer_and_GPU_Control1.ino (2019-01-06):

#include "Accelerometer_and_GPU_Control.h"

MPU6050 mpu6050(Wire);

double GyroX, GyroY,GyroZ;
double AccelX, AccelY, AccelZ;
double AccelPitchAngle = 0.0, AccelRollAngle = 0.0, AccelYawAngle = 0.0;

//A variable used to ensure frequency of sensor readings is constant
long FrequencyTimer;

bool InitialSetGyroAngles = false;

unsigned int PIDCounter = 0;

//PID Setup
double PitchSet = 0.0, RollSet = 0.0;
double PitchKp = 1.0, PitchKd = 0.15, PitchKi = 0.0;
double RollKp = 1.0, RollKd = 0.15, RollKi = 0.0;


double PitchOutput, RollOutput; //Output values from the PID that will be sent to the servos
//Servo position
double LeftServo;
double RightServo;

//Set up PID for pitch and yaw
PID PitchPID(&AccelPitchAngle, &PitchOutput, &PitchSet, PitchKp, PitchKi, PitchKd, DIRECT);
PID RollPID(&AccelRollAngle, &RollOutput, &RollSet, RollKp, RollKi, RollKd, DIRECT);

Servo Servo_1; //Servo for left steering
Servo Servo_2; //Servo for right steering

//Servo for wing retraction
Servo Servo_3;

//Collect all data
void ReadSensors(){

  mpu6050.update();
  
  GyroX  = mpu6050.getRawGyroX();
  GyroY  = mpu6050.getRawGyroY();
  GyroZ  = mpu6050.getRawGyroZ();
  /*
  AccelX = mpu6050.getRawAccX();
  AccelY = mpu6050.getRawAccY();
  AccelZ = mpu6050.getRawAccZ();
  */
  AccelX = mpu6050.getAccX();
  AccelY = mpu6050.getAccY();
  AccelZ = mpu6050.getAccZ();
   
  AccelPitchAngle = mpu6050.getAngleX();
  AccelRollAngle  = mpu6050.getAngleY();
  AccelYawAngle   = mpu6050.getAngleZ();
  
}

//Print the required variables for debug purposes
void ShowValues(){


  Serial.print("Pitch = "); Serial.print(AccelPitchAngle);
  Serial.print("\tRoll = ");  Serial.print(AccelRollAngle);
  //Serial.printf(" Roll Angle = "); Serial.println(AccelRollAngle);
  //Serial.printf("  Yaw Angle = ");  Serial.println(AccelYawAngle);
  //Serial.println("");
  
}

void setup() {
  
  Serial.begin(9200);
  pinMode(LED_BUILTIN, OUTPUT);
  Wire.begin(); //MPU6050 requires Wire for communication
  mpu6050.begin();
  mpu6050.update();
  mpu6050.calcGyroOffsets(true); //Take x readings, adding each one then divide the total by x. Take that value away from each further reading.

  Serial.println();
  Serial.println("Levelling system has been calibrated.");
  ReadSensors();

  //Connect all three servos (2 for steering and one for reeling in the folding wings
  Servo_1.attach(3);
  Servo_2.attach(2);
  Servo_3.attach(4); //wheeling control

  //Output limits ensure that values will not exceed that which the servo can take.
  PitchPID.SetOutputLimits(-90, 90);
  PitchPID.SetSampleTime(20);
  PitchPID.SetMode(AUTOMATIC);

  RollPID.SetOutputLimits(-90, 90);
  RollPID.SetSampleTime(20);
  RollPID.SetMode(AUTOMATIC);

  delay(1000);

}

void loop() {

  Serial.println("Hello World");
  
  digitalWrite(LED_BUILTIN, HIGH);   // turn the LED on (HIGH is the voltage level)

  //Routine for wing release
  ReadSensors();
  float MagAccel, PrevMagAccel, DifferenceAccel;
  //Collect the magnitude of acceleration
  PrevMagAccel = sqrt((AccelX * AccelX) + (AccelY*AccelY) + (AccelZ*AccelZ));

  //Wait until there is a large enough difference in accelerometer readings to release the wings
  while(1){

    ReadSensors();
    MagAccel = sqrt((AccelX * AccelX) + (AccelY*AccelY) + (AccelZ*AccelZ));

    DifferenceAccel = abs(MagAccel - PrevMagAccel);

    if (DifferenceAccel > 0.4){

      Serial.print("Difference = ");
      Serial.println(DifferenceAccel);
      //Go to servo position to release the wings
      Servo_3.write(135);
      break;
            
    }   

    delay(100);

  }
  
  Serial.println("Left first loop");
  delay(1000);
  Servo_3.write(10);
  delay(1000);
  
  //Enter stabilisation control loop
  while(1){

    FrequencyTimer = micros(); //micros is the amount of uS that the system has been running.

    ReadSensors();

    ShowValues();

    PitchPID.Compute();
    RollPID.Compute();

    //LeftServo = PitchOutput + 90;
    LeftServo  = (0.5 * RollOutput) + (0.5 * PitchOutput) + 90;
    RightServo = (0.5 * RollOutput) - (0.5 * PitchOutput) + 90;

    //Ensure that values sent to the servos will not be out of their working range
    if (LeftServo > 160){

      LeftServo = 160;
      
    }
    if (LeftServo < 45){

      LeftServo = 45;
      
    }
    if (RightServo > 160){

      RightServo = 160;
      
    }
    if (RightServo < 45){

      RightServo = 45;
      
    }

    Serial.print("\tPitchOut = "); Serial.print(PitchOutput);
    Serial.print("\tRollOut = "); Serial.println(RollOutput);
    Serial.println();
    //Go to calculated servo positions
    Servo_2.write(LeftServo);
    Servo_1.write(RightServo);

    while((micros() - FrequencyTimer) < 20000){ //wait until frequency of 50Hz (1/20000) has been reached.
    
    }
    //Take next frequency timer reading to reset it
    FrequencyTimer = micros();
    
  }
  
}

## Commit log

2019-01-06 Add files via upload
    The code that implements the stabilised control of the glider after releasing the wings.
    [Accelerometer_and_GPU_Control1.ino]
2019-01-06 Add files via upload
    The Schematic detailing the pin connections for the servos and the MPU6050
